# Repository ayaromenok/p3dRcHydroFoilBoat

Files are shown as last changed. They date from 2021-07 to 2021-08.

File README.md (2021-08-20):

# 3D printed Radio Controlled Hydrofoil boat

## Table of Contents

 - [Introduction](#intro)
 - [Status - on hold](#on_hold)
 - [Version v0.3.0](#v0_3_0)
 - [Version v0.2.0](#v0_2_0)
 - [Version v0.1.1](#v0_1_1)

## Introduction

Hydrofoil boat (called "Meteor" in tribute of Rostislav Alexeev hydrofoil ship) with trimaran structure and differentional trust mix props.
Impelented in OpenSCAD. To rebuild STL's required [p3d Lib2 0.2.2.20210615](https://github.com/ayaromenok/p3dLib)

## Status - on hold

Due to instability of boat in hydrofoil mode current development is put on hold. New ideas about form of wing required

## v0.3.0 

- Version from 2021.08.20

### Issues
  - stability issues in hydrofoil mode
  - CoPET printed floats not hydroscopic

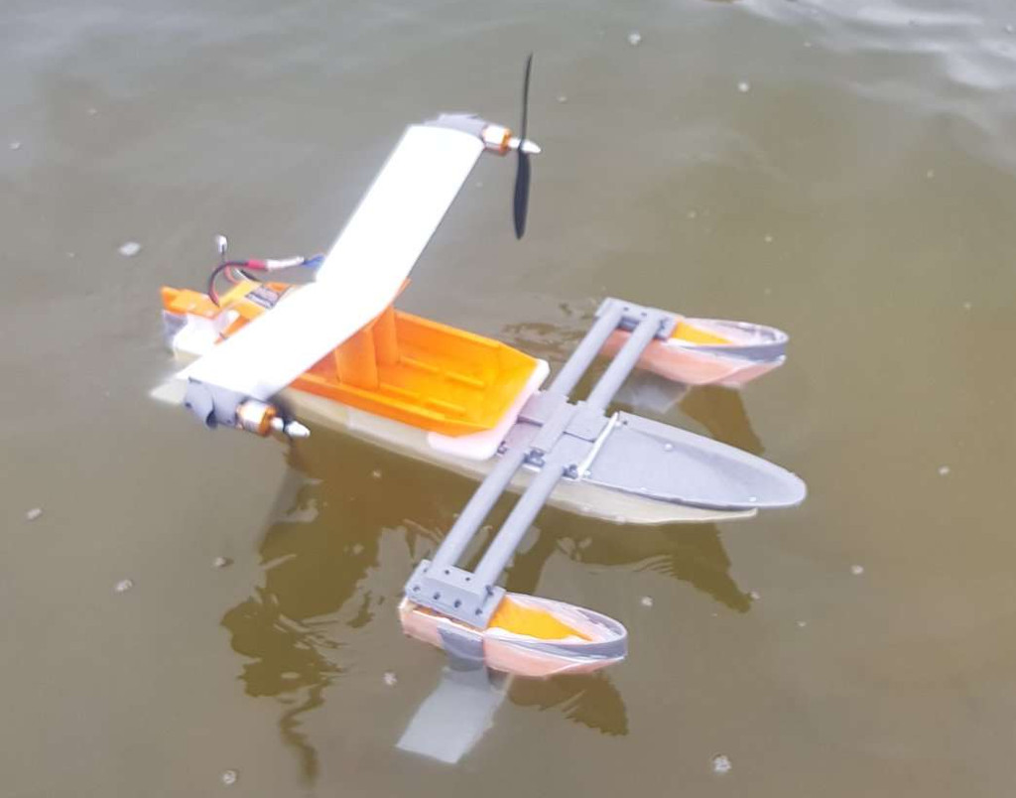
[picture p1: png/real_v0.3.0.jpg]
    
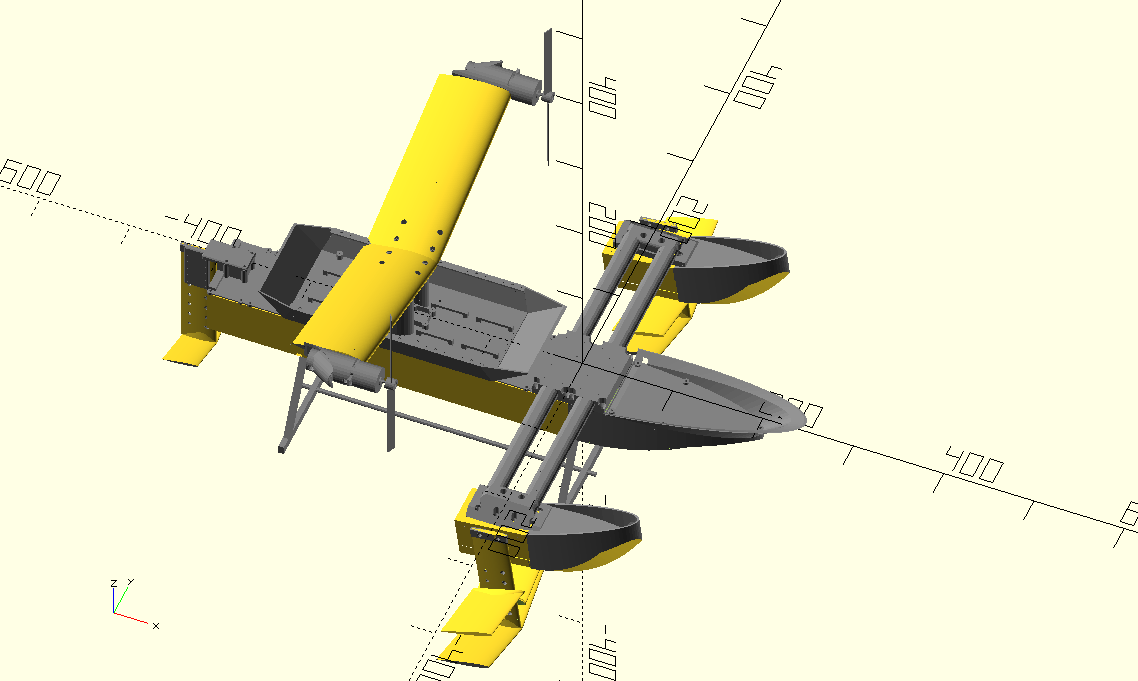
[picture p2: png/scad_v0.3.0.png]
    

## v0.2.0 

- Version from 2021.07.23

### Issues    
  - support float/hydrofoil connetors need to be higher(affected by water)
  - line of support floats and engine should be in one line (spray affected props)
  - front connectors should be stronger
  - front floats should be installed in 10-15 degree
  - front wing can be bigger
  - camera connector should be mounted a top of the engine wings and be strong
  - nose gunwale(falschbort) should be much higher for strong wind situation
  
[video from ground](https://www.youtube.com/watch?v=aogEewLZsBY)
[onboard video](https://www.youtube.com/watch?v=OHG-W-Ka8qo)

## v0.1.1 

- Version from 2021.07.18

### Issues
  - waterproofness of right support float (printing issue)
  - small support floats [issue #8](https://github.com/ayaromenok/p3dRcHydroFoilBoat/issues/8)
  - support floats should be moved forward [issue #9](https://github.com/ayaromenok/p3dRcHydroFoilBoat/issues/9)
  - fuselage strength and connection need to be revisioned [issue #10](https://github.com/ayaromenok/p3dRcHydroFoilBoat/issues/10)
  - support for Jetson Nano carrier board required (wider fuselage required) [issue #10](https://github.com/ayaromenok/p3dRcHydroFoilBoat/issues/10)
  - support for Raspberry Pi required [issue #10](https://github.com/ayaromenok/p3dRcHydroFoilBoat/issues/10)
  
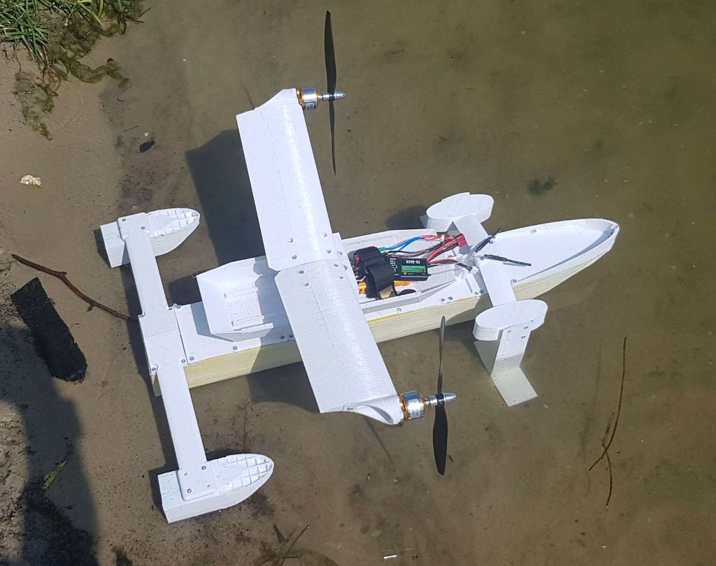
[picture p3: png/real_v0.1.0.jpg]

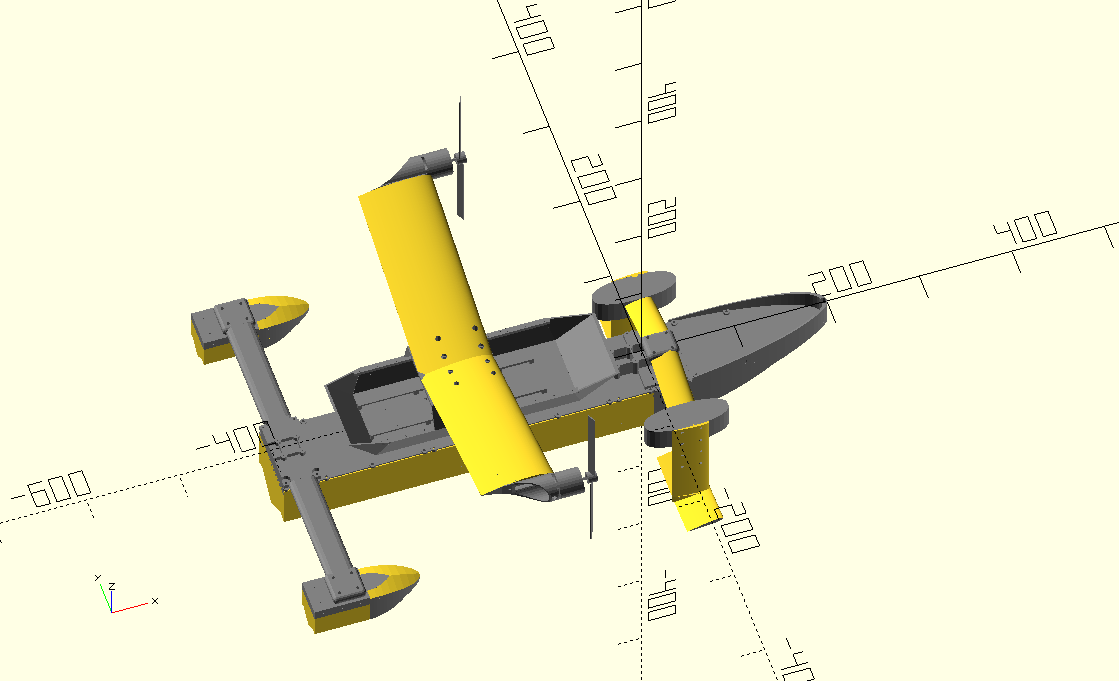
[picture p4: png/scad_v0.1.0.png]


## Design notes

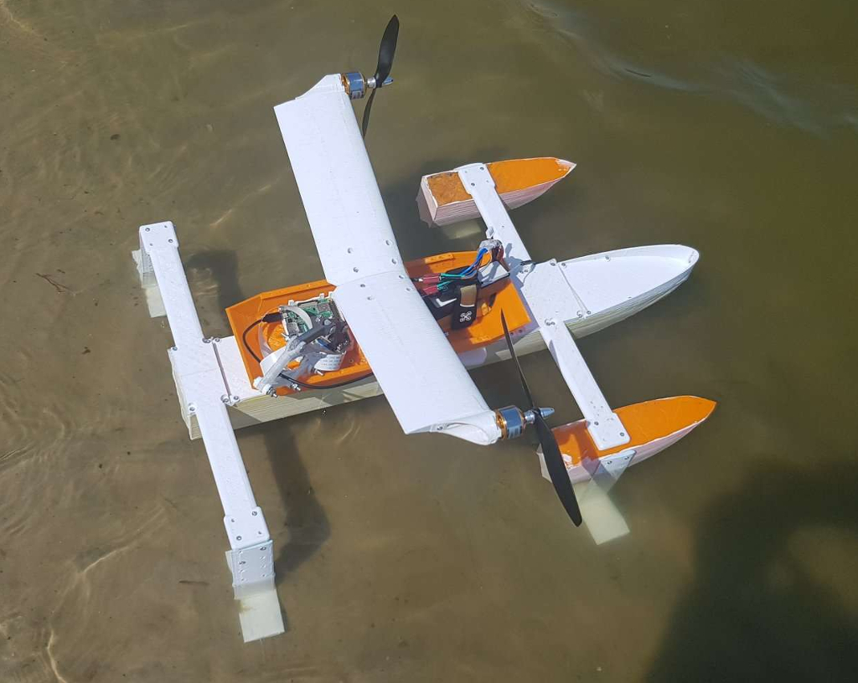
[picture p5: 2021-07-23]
png/real_v0.2.0.jpg

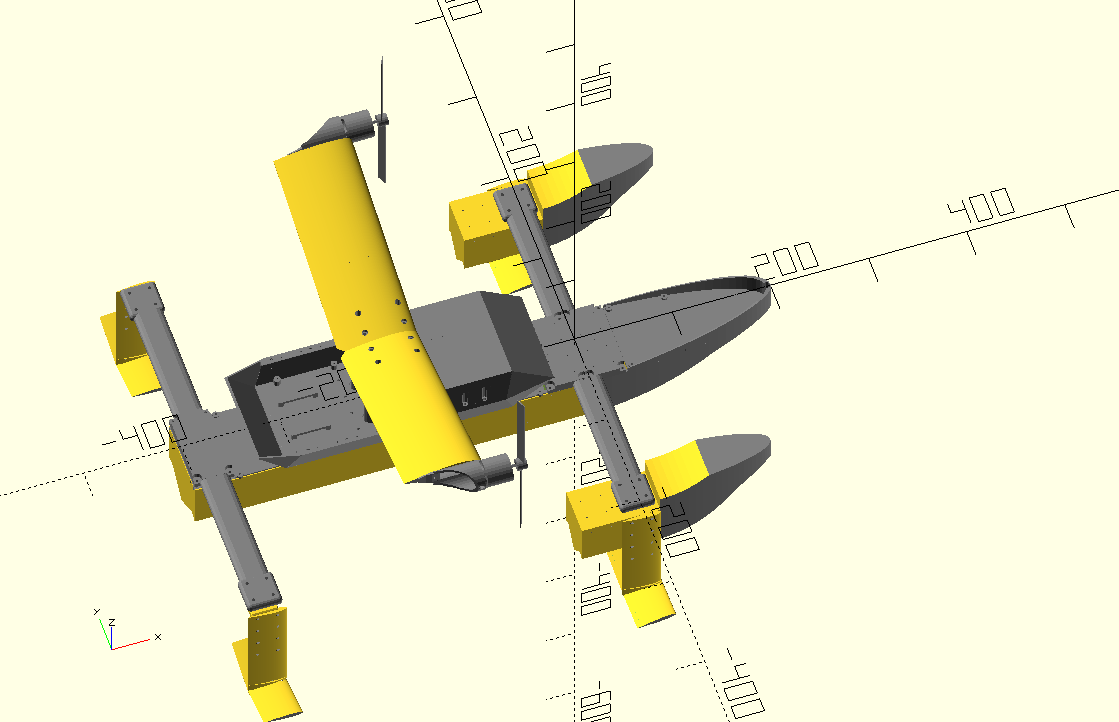
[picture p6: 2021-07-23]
png/scad_v0.2.0.png

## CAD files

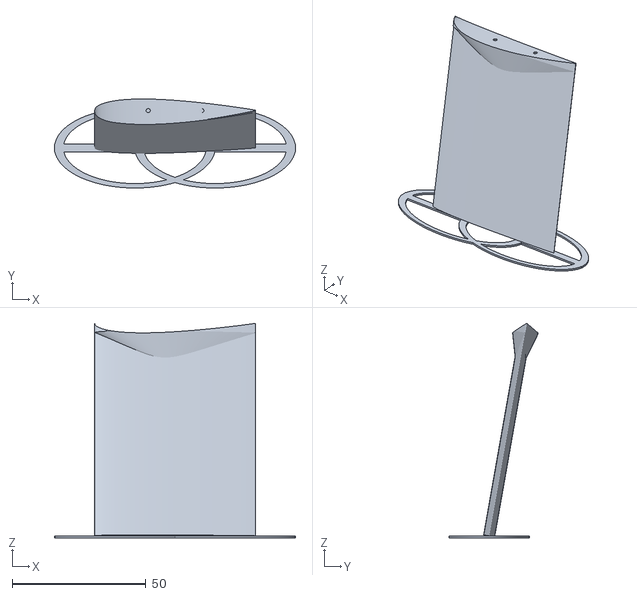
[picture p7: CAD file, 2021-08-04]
stl/wingHalf_80x60mm_L.stl
90.0 x 33.2 x 80.2

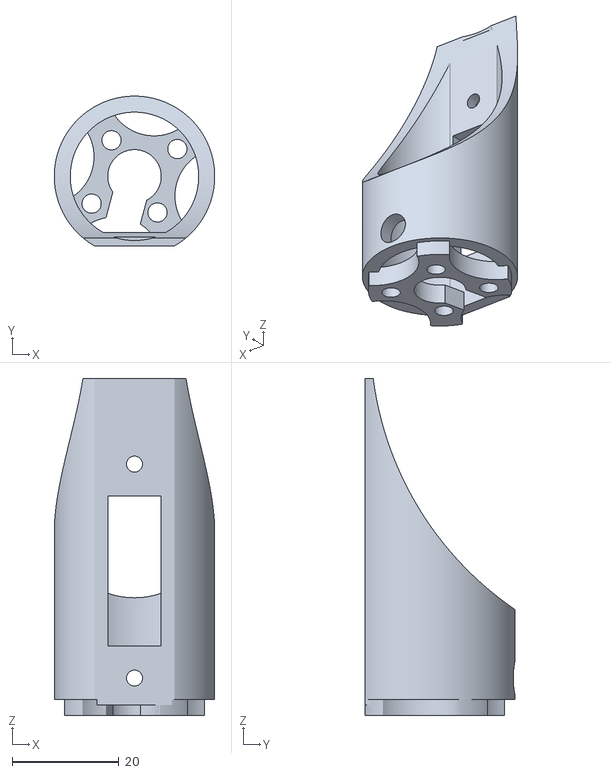
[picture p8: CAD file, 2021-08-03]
stl/engine2212_mount.stl
30.0 x 28.0 x 63.0

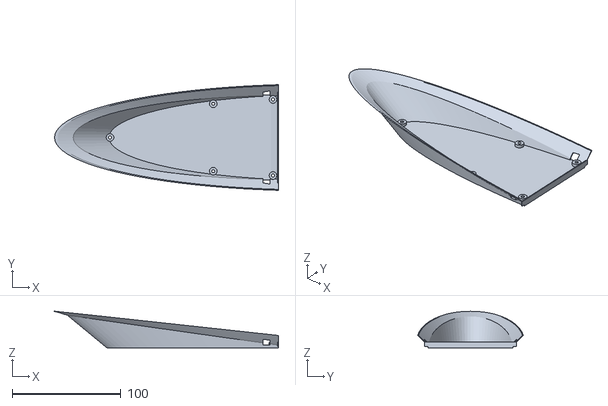
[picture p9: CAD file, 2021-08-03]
stl/floatsHiSpeed_v2_front_top.stl
206.2 x 97.3 x 33.6

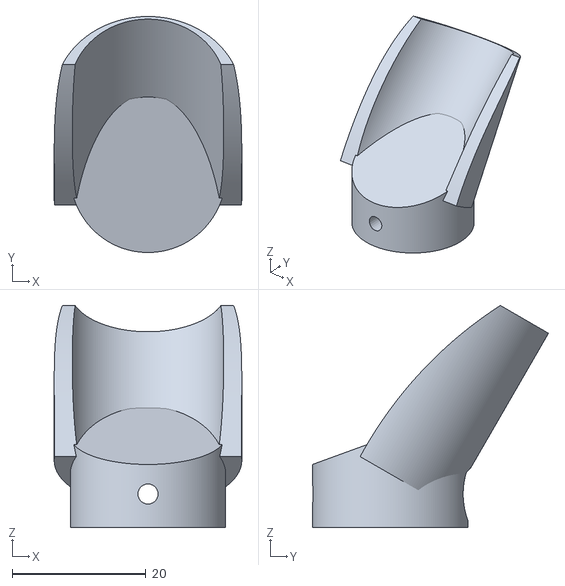
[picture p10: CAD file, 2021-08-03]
stl/dual2212MotorMount_ESC_air_intake.stl
28.0 x 35.2 x 33.1

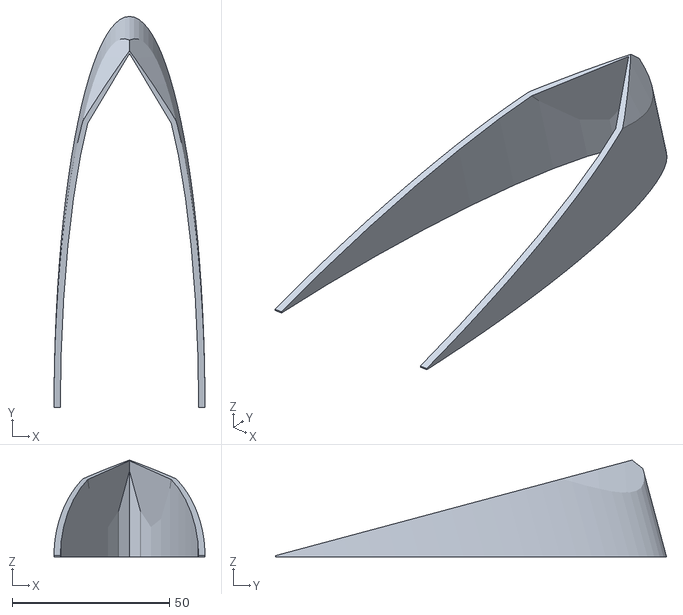
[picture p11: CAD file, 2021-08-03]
stl/floatsSupport_top.stl
48.0 x 124.3 x 30.8

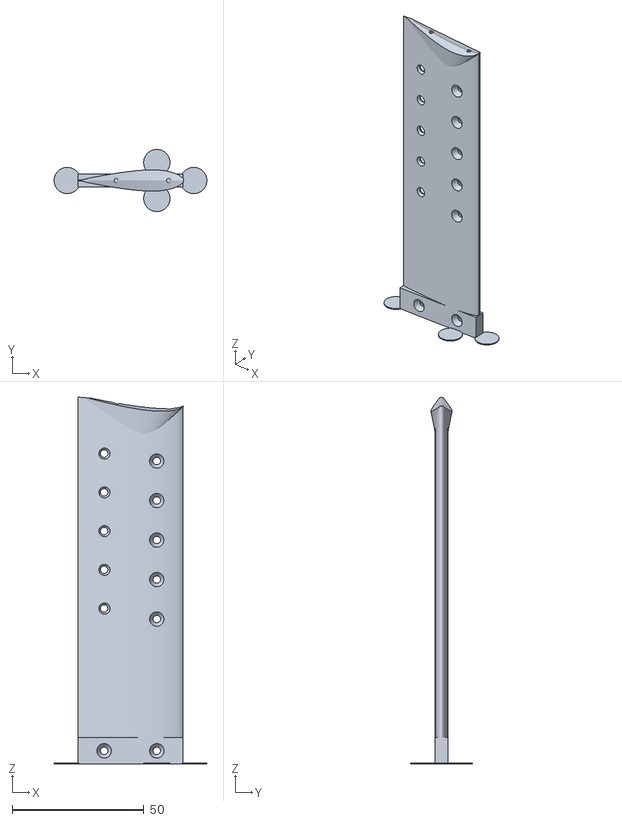
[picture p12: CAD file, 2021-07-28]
stl/wingHolder_140mm.stl
58.0 x 23.6 x 139.3

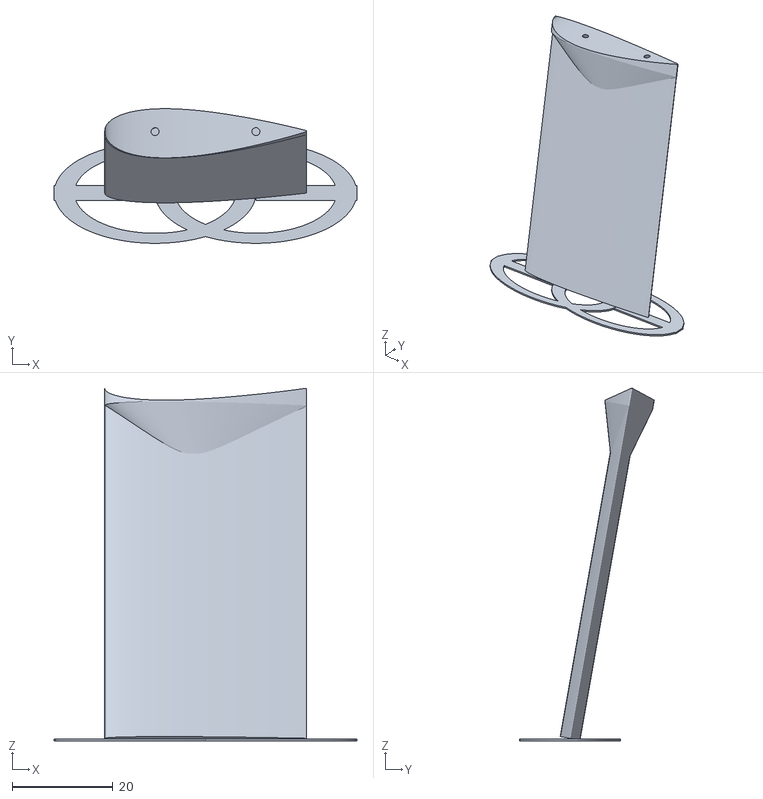
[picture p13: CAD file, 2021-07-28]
stl/wingHalf_70x40mm_L.stl
60.0 x 26.7 x 70.0

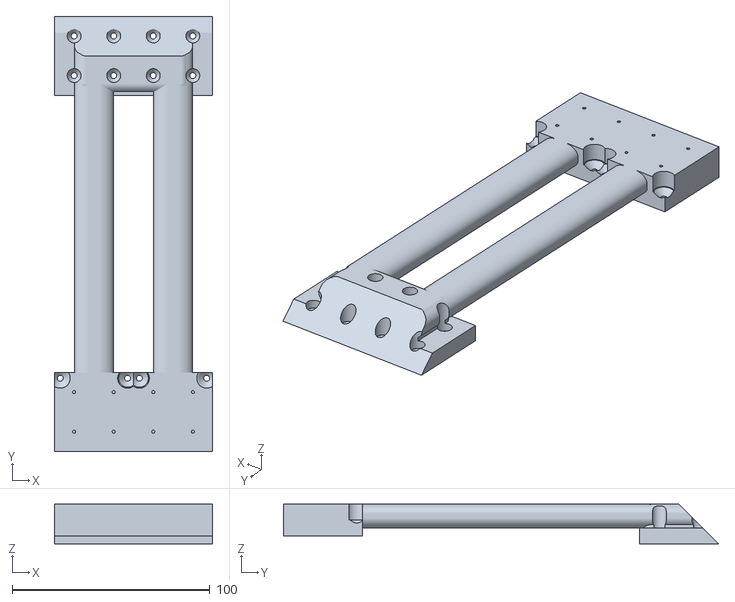
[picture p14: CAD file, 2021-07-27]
stl/floatsSupportFront_v3.stl
80.0 x 219.9 x 20.0

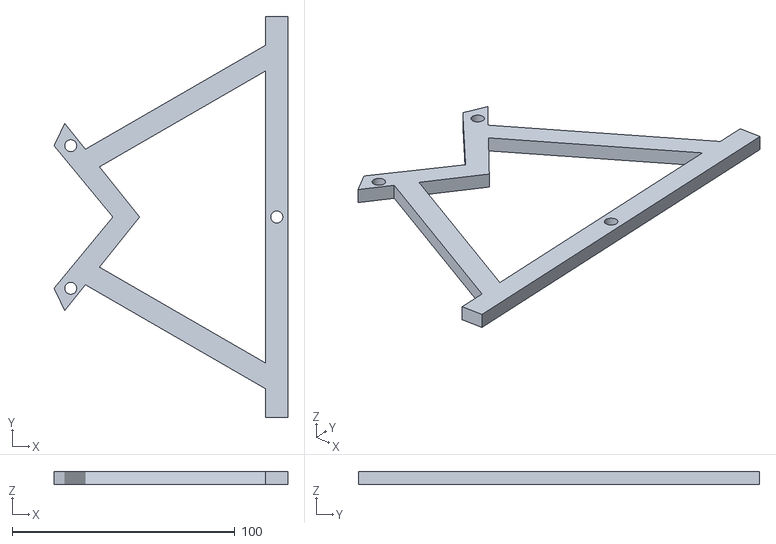
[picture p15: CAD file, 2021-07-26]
stl/floatsHiSpeed_v2_holder.stl
105.0 x 180.0 x 6.00

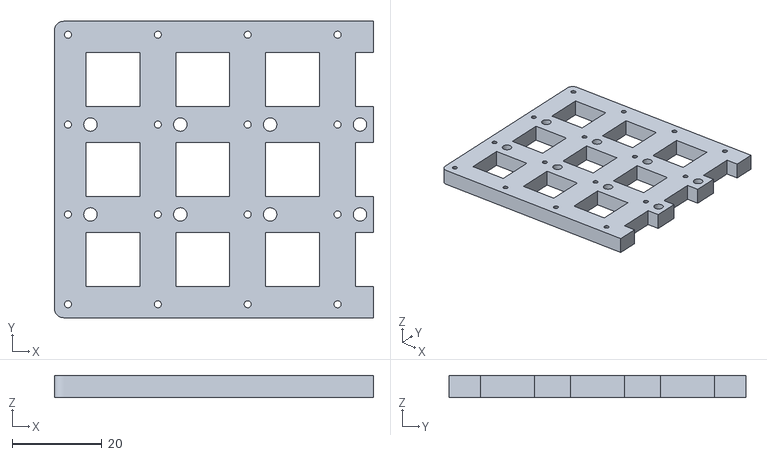
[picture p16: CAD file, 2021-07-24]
stl/fuselage_v2_front_back_support.stl
71.0 x 66.0 x 5.00

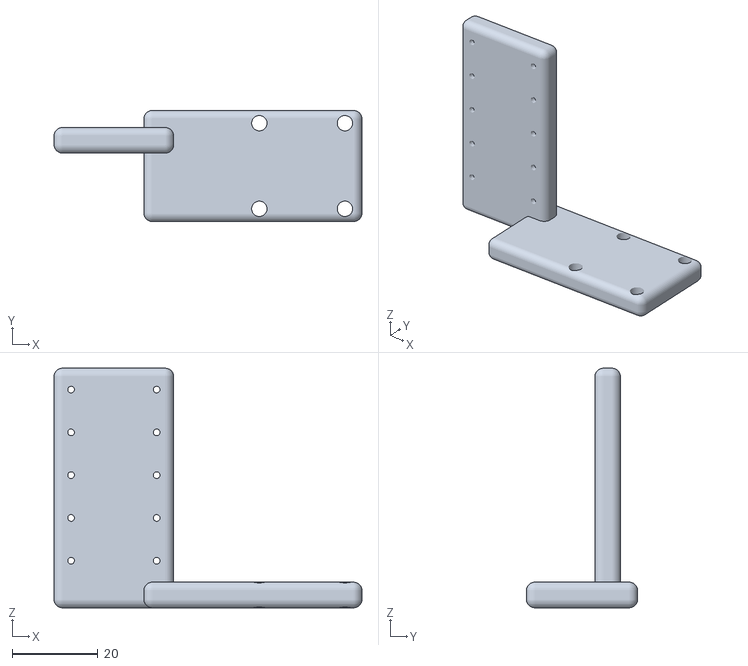
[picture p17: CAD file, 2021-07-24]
stl/wingHolderBack.stl
72.0 x 26.0 x 56.0

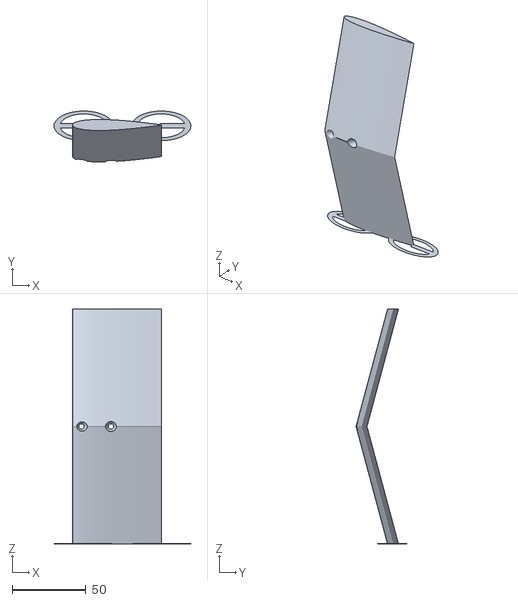
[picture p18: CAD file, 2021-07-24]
stl/wing_V15_160x60mm.stl
92.5 x 34.4 x 159.0

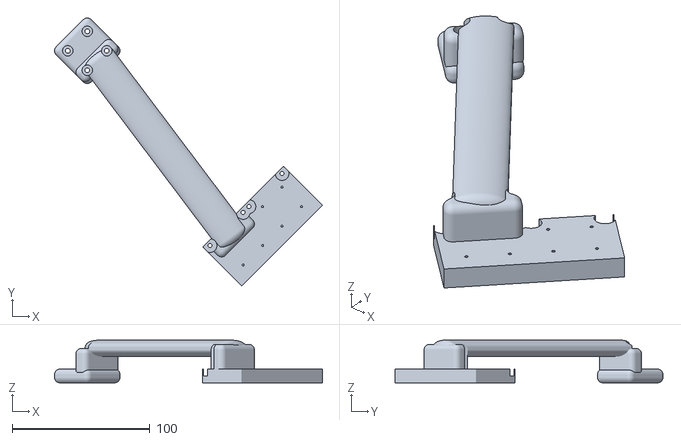
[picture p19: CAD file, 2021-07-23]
stl/floatsSupportFront_v2_mirrored.stl
194.6 x 194.6 x 31.0

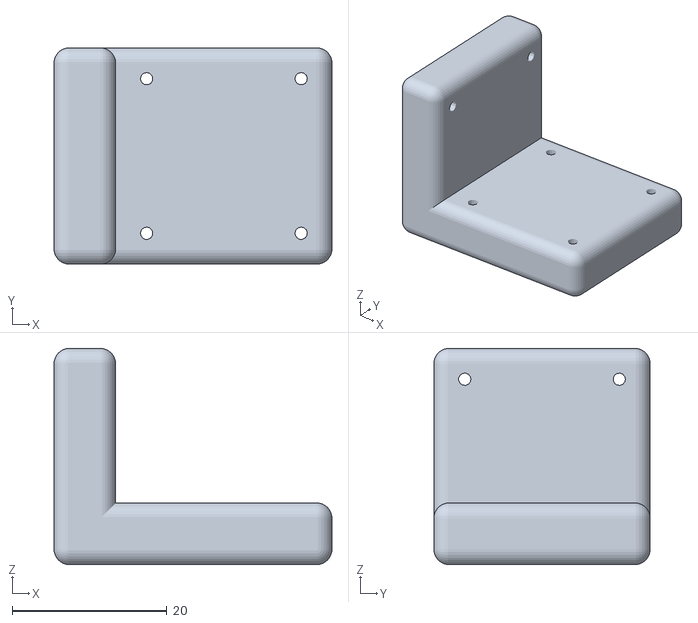
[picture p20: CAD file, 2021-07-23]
stl/floatsSupportConnector_L.stl
36.0 x 28.0 x 28.0

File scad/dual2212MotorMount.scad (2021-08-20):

include <../../lib/lib2.scad>
include <../../lib/lib2/ext/motor.scad>
include <../../lib/lib2/ext/prop.scad>
include <../../lib/lib2/ext/servo.scad>


//engine2212_wing();
//engine2212_mount(isMetal=false);
//engine2212_mount_ESC_air_intake();
//engine2212_mount_ESC_air_intake(27,-220,0,  0,-90,0);
//2print
//engine2212_wing(rx=-90,isAdhesion=true);//left
//engine2212_wing(rx=90,my=1,isAdhesion=true);//right
//engine2212_mount(ry=90);//left
//engine2212_mount(ry=90, my=1);//right

function naca_half_thickness(x,t) = 5*t*(0.2969*sqrt(x) - 0.1260*x - 0.3516*pow(x,2) + 0.2843*pow(x,3) - 0.1015*pow(x,4));
function naca_top_coordinates(t,n) = [ for (x=[0:1/(n-1):1]) [x, naca_half_thickness(x,t)]];
function naca_bottom_coordinates(t,n) = [ for (x=[1:-1/(n-1):0]) [x, - naca_half_thickness(x,t)]];
function naca_coordinates(t,n) = concat(naca_top_coordinates(t,n), naca_bottom_coordinates(t,n));

module engine2212_mount_ESC_air_intake(px=0,py=0,pz=0, rx=0,ry=0,rz=0, mx=0,my=0,mz=0, isMetal=false, isAdhesion=false){
    translate([(px), (py), pz])
    rotate([rx,ry,rz])
    mirror([mx,my,mz]){  
        difference(){
            yCyl(11.6,30, 0,218,27,  0,90,0);            
            yCyl(4,20,  -10,220,27,   90,0,0);
            yCyl(1.5,40,  -10,218,27,   90,0,0);
            yCube(20,50,25,  10,220,27,   0,0,-20);
        }//difference
        
        difference(){
            difference(){
                yCyl(14,30, 8,222,27,  -30,90,0);
                yCyl(11.6,35, 11.4,222,27,  -45,90,0);
            }//difference
            difference(){
                yCube(150,150,40, -34,268,27);
                yCyl(62,50, -34,268,27,  0,0,0);
            }//difference
            yCyl(4,20,  -10,220,27,   90,0,0);
        }//difference
        
    }//transform
}//module

module engine2212_mount(px=0,py=0,pz=0, rx=0,ry=0,rz=0, mx=0,my=0,mz=0, isMetal=false, isAdhesion=false){
    translate([(px), (py), pz])
    rotate([rx,ry,rz])
    mirror([mx,my,mz]){  
        translate([50,218,27])
        rotate([0,90,0]){            
                if (isMetal){
                    blMotor2212(0,0,0 ,0,0,-22.5-10);            
                    prop8060(0,0,25,   0,0,0);      
                }//isMetal    
                difference(){
                    union(){
                        blMotor2212_bot(0,0,0, 0,0,-22.5-10);   
                        yTube(15,12,60, 0,0,-26-20,  0,0,0);
                        yCube(14,5,60,    0,-13,-45);
                    }//union                
                    yCyl(62,40, -0,50,-84,  0,90,0);
                    yCube(20,20,100,    0,-23,-50);
                    //holes - to engine mount            
                    yCyl(1.5,50,    0,0,-20,  90,0,0);
                    yCyl(1.5,50,    0,0,-60,  90,0,0);
                    yCyl(3,30,    0,20,-20,  90,0,0);
                    //
                    yCube(6.5,6,10, 1.5,-6,-15, 0,0,15);
                    yCube(10,10,28, 0,-10,-40, 0,0,0);
                    //yCube(6,10,18, 8.5,-10,-70, 0,17,0);
                    //yCube(6,10,18, -8.5,-10,-70, 0,-17,0);
                }//difference            
                
        }//translate        
    }//transform
}//module                

module engine2212_wing(px=0,py=0,pz=0, rx=0,ry=0,rz=0, mx=0,my=0,mz=0, isMetal=false, isAdhesion=false){
    translate([(px), (py), pz])
    rotate([rx,ry,rz])
    mirror([mx,my,mz]){  
        chord=80;
        length=210;
        difference(){
            union(){
                translate([chord/2,length/2,0])
                rotate([75,0,180])
                linear_extrude(height=length, center=true) {                    
                    points = naca_coordinates(t=0.22,n=300);
                    scale([chord,chord,1])
                        polygon(points);
                } //translate        
                
            }//union
            //cable to engine
            yCube(28,length+10,12,   10,length/2,0,  15,0,0);
            //vertical/horizontal geometry
            yCube(chord*2, chord,chord, 0,length+chord/2-5,0);
            yCube(chord*2, chord,chord, 0,-chord/2+5,0);            
            yCube(chord*2, chord,chord, 0,chord/2-5,-chord/2-25);
            
            //holes - to fuselage
            yCyl(1.8,70,    30,15,0);
            yCyl(1.8,70,    -10,15,0);
            yCyl(1.8,70,    30,35,0);
            yCyl(1.8,70,    -10,35,0);
        
            yCyl(3,20,    30,15,-10);
            yCyl(3,20,    -10,15,-10);
            yCyl(3,20,    30,35,-10);
            yCyl(3,20,    -10,35,-10);
            //holes - to engine mount            
            yCyl(0.8,50,    30,length,27,  90,0,0);
            yCyl(0.8,50,    -10,length,27,  90,0,0);
            
        }//difference
        
        if (isMetal){
            translate([50,length+9,27])
            rotate([0,90,0]){            
                blMotor2212(0,0,0 ,0,0,-22.5-10);            
                prop8060(0,0,25,   0,0,0);      
            
                //blMotor2212_bot(0,0,0, 0,0,-22.5-10);   
                //yTube(14,12,20, 0,0,-26,  0,0,0);
            }//translate
        }//isMetal
        if(isAdhesion){
            yCyl(5,0.7,    30,length-5.3,15,  90,0,0);
            yCyl(5,0.7,    -10,length-5.3,17,  90,0,0);
            yCyl(5,0.7,    -40,length-5.3,25,  90,0,0);        
        }//isAdhesion            
    }//transform
}//module                


//engine2212_basket_inch5_assembly();

//2print
//engine2212_basket_inch5_front();
//engine2212_basket_inch5_back();
//engine2212_support(0,0,0, 0,0,45);
//engine2212_basket_inch5_rudder(0,0,0, 0,90,90, isAdhesion=true);
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

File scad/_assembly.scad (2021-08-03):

include <hydrofoil.scad>
include <floatsHiSpeed_v2.scad>
include <dual2212MotorMount.scad>
include <fuselage_v2.scad>
include <floatsSupport.scad>

floatHiSpeed_v2_assmebly(0,0,39.5, 0,0,-90);
//float holder
floatHiSpeed_holder(0,0,-66, 0,90,90);
floatHiSpeed_holder(-300,0,-66, 0,90,90);
yCyl(2.5,330,   -150,0,-165,  0,90,0);

//engine wing
fuselage_engine_support(-200,0,-15);
engine2212_wing(-200,-5,110 );
engine2212_wing(-200,5,110, my=1);
engine2212_mount(-200,-5,110,isMetal=true);
engine2212_mount(-200,5,110,isMetal=true, my=1);
engine2212_mount_ESC_air_intake(-200,-5,110);
engine2212_mount_ESC_air_intake(-200,5,110, my=1);


//front hydro-wing
floatSupportWingFront_v3(0,0,-20, mx=1);
floatSupportWingFront_v3(0,0,-20, rz=180, mx=0);
floatSupport(20,-200,53,  7,0,-90);
floatSupport(20,200,49,  7,0,-90);
floatSupport_top(20,-200,53,  7,0,-90);
floatSupport_top(20,200,49,  7,0,-90);
wingMainNACA_multy_V_v2(7,-230,-164, 0,-7,0);
wingMainNACA_multy_V_v2(7,230,-164, 0,-7,0, 0,1,0);
//wingMainNACA_V(20,187,-133, 90,10,180, length=160,chord=60);
//wingHolderSingle(0,226,-145,  180,190,180, length=120);

//wingMainNACA_V(20,-265,-133, 90,10,180, length=160,chord=60);
//wingHolderSingle(0,-226,-145,  180,180,180, length=120);

//back hydro-wing
wingHolderBack(-385, rx=180);
wingMainNACA_V(-405,-25,-132,rx=90,ry=8, rz=180, isAdhesion=false, length =100, chord=40);
wingHolderSingle(-425,0,-143,isAdhesion=false);

//fuselage
//fuselage_front_back_support(-200,0,2.5);
fuselage_front(-200,0,-10);
fuselage_back(-310,0,-10);

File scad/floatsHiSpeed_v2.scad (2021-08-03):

include <../../lib/lib2.scad>

//2print rotated in Y axis for better print
//floatHiSpeed_front_v2(pz=-60,ry=-90,rz=0);
//floatHiSpeed_front_top_v2(ry=-90,rz=0);
//floatHiSpeed_center_v2(pz=-60,ry=-90,rz=0);
//floatHiSpeed_front_top_v2_1(ry=-90,rz=90);
//floatHiSpeed_front_top_v2_1_1(ry=-90,rz=90);
//floatHiSpeed_front_top_v2_1_1(-42,0,0, 90,(90-6.2),0);
//floatHiSpeed_front_top_v2_1_1(-42,0,0, 90,-90,0);
//floatHiSpeed_front_top_v2_1_2(ry=-90,rz=0);
//floatHiSpeed_center_top_v2_1(ry=-90,rz=0);
//floatHiSpeed_center_top_v2_3(ry=-90,rz=0);
//floatHiSpeed_v2_assmebly();

//floatHiSpeed_holder(rx=90);

module floatHiSpeed_holder(px=0,py=0,pz=0, rx=0,ry=0,rz=0){
    translate([(px),(py),pz])
    rotate([rx,ry,rz]){
            difference(){                                        
                scale([1.2,1,1])            
                rotate([90,0,0])
                linear_extrude(6)
                    polygon( points=[[0,32],[22,0],[0,-32], [4,-42],[32,0], [4,42]]);
                yCyl(2.7,20,    7.5,0,32,  90,0,0);
                yCyl(2.7,20,    7.5,0,-32,  90,0,0);
            }//difference
        yCube(100,6,10,  58,-3,50, 0,-30,0);
        yCube(100,6,10,  58,-3,-50,  0,30,0);
        difference(){    
            yCube(10,6,180,  100,-3,0);    
            yCyl(2.7,20,    100,0,0,  90,0,0);    
        }//difference
    }//transform
}//module                    
module floatHiSpeed_v2_assmebly(px=0,py=0,pz=0, rx=0,ry=0,rz=0){
    translate([(px),(py),pz])
    rotate([rx,ry,rz])
        rotate([0,90,0])
    {
        floatHiSpeed_front_v2();//132
        //floatHiSpeed_front_top_v2();
        floatHiSpeed_center_v2();
        floatHiSpeed_center_v2(0,-200,0);
        floatHiSpeed_front_top_v2_1_1(142,0,0,    0,180);
        //floatHiSpeed_front_top_v2_1_2(142,0,0,    0,180);
        floatHiSpeed_center_top_v2_1(142,0,0,    0,180);
        floatHiSpeed_center_top_v2_2(142,-200,0,    0,180);
        floatHiSpeed_center_top_v2_1(142,-200,0,    0,180);
        floatHiSpeed_center_top_v2_3(142,-400,0,    0,180);
    }//transform
}//module


module floatHiSpeed_center_top_v2_3(px=0,py=0,pz=0, rx=0,ry=0,rz=0){
    translate([(px),(py),pz])
    rotate([rx,ry,rz])    
    {
        difference(){
            floatHiSpeed_center_top_v2_2();
            yCube(30,50,100,   90,-25);
        }
    }//transform
}//module


module floatHiSpeed_center_top_v2_1(px=0,py=0,pz=0, rx=0,ry=0,rz=0){
    translate([(px),(py),pz])
    rotate([rx,ry,rz])    
    {
    difference(){        
            yCube(3,116,78,    82,-100,0);
            //connectors            
            yCyl(1.5,26,  80,-47,37, 0,90,0);
            yCyl(1.5,26,  80,-47,-37, 0,90,0);
            yCyl(1.5,26,  80,-103,37, 0,90,0);
            yCyl(1.5,26,  80,-103,-37, 0,90,0);          
            yCyl(1.5,26,  80,-153,37, 0,90,0);
            yCyl(1.5,26,  80,-153,-37, 0,90,0); 
        }//difference
        yTube(3.5,1.5,3,  83,-47,37, 0,90,0);
        yTube(3.5,1.5,3,  83,-47,-37, 0,90,0);
        yTube(3.5,1.5,3,  83,-103,37, 0,90,0);
        yTube(3.5,1.5,3,  83,-103,-37, 0,90,0);          
        yTube(3.5,1.5,3,  83,-153,37, 0,90,0);
        yTube(3.5,1.5,3,  83,-153,-37, 0,90,0); 
        
    }//transform
}//module



module floatHiSpeed_center_top_v2_2(px=0,py=0,pz=0, rx=0,ry=0,rz=0){
    translate([(px),(py),pz])
    rotate([rx,ry,rz])    
    {
    difference(){        
            yCube(3,84,78,    82,0,0);
            //connectors            
            yCyl(1.5,26,  80,37,37, 0,90,0);
            yCyl(1.5,26,  80,37,-37, 0,90,0);
            yCyl(1.5,26,  80,3,37, 0,90,0);
            yCyl(1.5,26,  80,3,-37, 0,90,0);          
            yCyl(1.5,26,  80,-3,37, 0,90,0);
            yCyl(1.5,26,  80,-3,-37, 0,90,0); 
            yCyl(1.5,26,  80,-37,37, 0,90,0);
            yCyl(1.5,26,  80,-37,-37, 0,90,0);          
        
        }//difference
        yTube(3.5,1.5,3,  83,37,37, 0,90,0);
        yTube(3.5,1.5,3,  83,37,-37, 0,90,0);
        yTube(3.5,1.5,3,  83,3,37, 0,90,0);
        yTube(3.5,1.5,3,  83,3,-37, 0,90,0);          
        yTube(3.5,1.5,3,  83,-3,37, 0,90,0);
        yTube(3.5,1.5,3,  83,-3,-37, 0,90,0); 
        yTube(3.5,1.5,3,  83,-37,37, 0,90,0);
        yTube(3.5,1.5,3,  83,-37,-37, 0,90,0);          
        yCube(5,16,70,    85.5,,-0);
        for (i=[-30:20:40]){
            yTube(3.5,0.7,20,    92.5,i,10, 0,90,0);
            yTube(3.5,0.7,20,    92.5,i,-10,0,90,0);
            yCube(20,1,18,    92.5,i,0);
            yCube(20,1,18,    92.5,i,00);
         }//for
         for (i=[-20:20:20]){
            yCube(20.0,18,1,    92.5,i,10);
            yCube(20.0,18,1,    92.5,i,-10);
         }//for    
    }//transform
}//module

module floatHiSpeed_front_top_v2_1_1(px=0,py=0,pz=0, rx=0,ry=0,rz=0){
    translate([(px),(py),pz])
    rotate([rx,ry,rz])    
    {
        difference(){
            union(){
                yCyl(0,33, 98,0,0,  0,90,0, $fn=100, sy=5,rb=40, rt=48);
                yCyl(0,10, 84,0,0,  6,90,0, $fn=100, sy=5,rb=40, rt=50);                
            }//union
            yCyl(0,32, 100,0,0,  0,90,0, $fn=100, sy=5, rb=39.6,rt=47.6);
            yCyl(0,10.2, 84,0,0,  6,90,0, $fn=100, sy=5.03,rb=39.2, rt=49.2);
            yCube(130,370,150,    108,-143,0);
            yCube(30,250,150,    119,144,0, 0,0,-6.2);
            //connectors
            yCyl(3.5,26,  98,196,0, 0,90,0);
            yCyl(1.4,26,  80,197,0, 0,90,0);
            yCyl(1.4,26,  80,102,31, 0,90,0);
            yCyl(1.4,26,  80,102,-31, 0,90,0);
            yCyl(1.4,26,  80,47,35, 0,90,0);
            yCyl(1.4,26,  80,47,-35, 0,90,0);          
            //water pass
            yCube(5,6,86,    86.5,53,0);
            //top light
            yCyl(2,100, 111,155,0, 0,0,0);
            yCyl(3,100, 110,145,0, 0,0,0);
            yCyl(2,100, 108,135,0, 0,0,0);
        }//difference
        //central support section
        /*difference(){
            yCube(30,152,2,    97,118,0);
            yCube(30,250,150,    119,144,0, 0,0,-6.2);
        }//difference
        */
        yTube(3.5,1.4,3,  85,197,0, 0,90,0);
        yTube(3.5,1.4,3,  85,102,31, 0,90,0);
        yTube(3.5,1.4,3,  85,102,-31, 0,90,0);
        yTube(3.5,1.4,3,  85,47,35, 0,90,0);
        yTube(3.5,1.4,3,  85,47,-35, 0,90,0);
        yCube(4,0.7,85,    84.8,42.3,0);        
        
        //yCube(5,80,5,    105,105,39, 0,45,-17);
    }//transform
}//module
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

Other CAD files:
stl/wingHalf_80x60mm_R.stl
stl/wingHalf_70x40mm_R.stl
stl/fuselage_v2_back.stl
stl/fuselage_v2_front_top.stl
scad/floatsSupport.scad
scad/floatsSupport_v2.scad
scad/fuselage.scad
scad/fuselage_v2.scad
scad/hydrofoil.scad
stl/engine2212_wing_left.stl
stl/engine2212_wing_right.stl
stl/floatsSupport.stl
stl/floatsSupportFront.stl
stl/floatsSupportFront_v2.stl
stl/floatsSupportWIng.stl
stl/floatsSupportWingFront.stl
stl/fuselage_back_bot.stl
stl/fuselage_front_bot.stl
stl/fuselage_v2_engine_support.stl
stl/fuselage_v2_front.stl
stl/wingChassis.stl
stl/wingHolder_120mm.stl
stl/wing_V15_100x40mm.stl

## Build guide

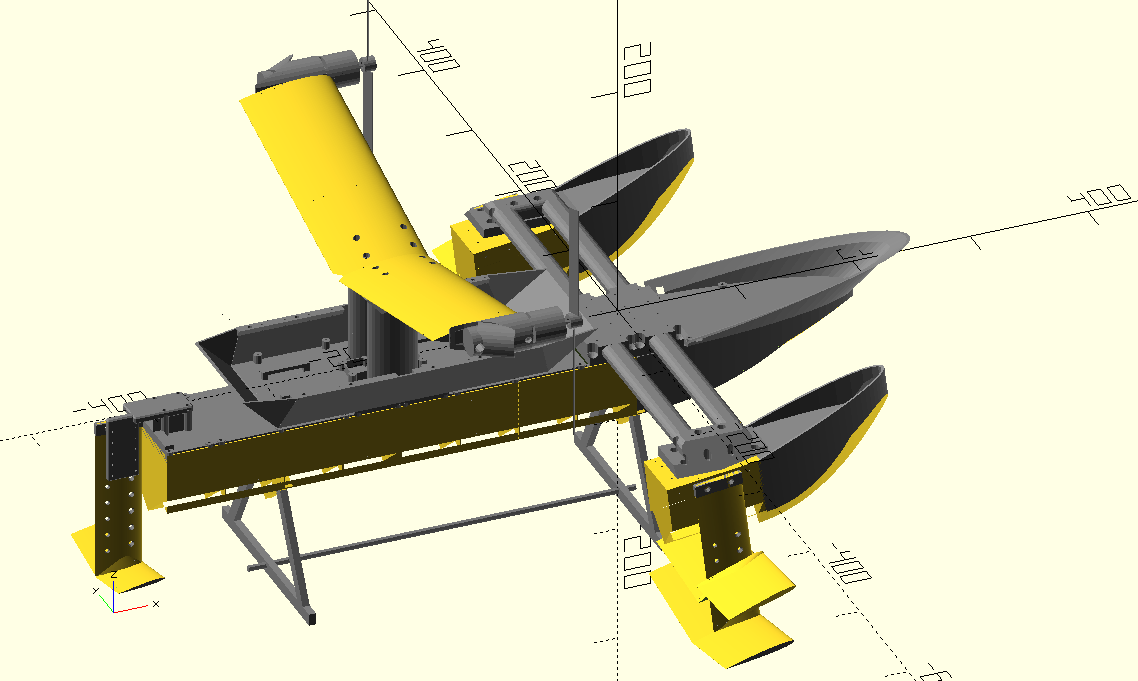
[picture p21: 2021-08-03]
png/_assembly.png

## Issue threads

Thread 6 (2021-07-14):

Fuselage for dual engine mount

ayaromenok, 2021-07-14:
can be connected to single or dual float configuration

ayaromenok, 2021-07-17:
need to review bottom section(thickness and connectors),
 make it more wide(to hold nvidia jetson nano)

Closed 2021-07-18.

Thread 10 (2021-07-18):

new fuselage (V2)

ayaromenok, 2021-07-18:
- better connector to main float
- Jetson nano carrier board connector
- Raspberry Pi  board connector

Closed 2021-07-23.

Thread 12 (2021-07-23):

higher angled connector to suppor floats/wings

ayaromenok, 2021-07-23:
- Current affected to much by the water/sprays from nose
- angle to floats need to be added on front

Closed 2021-07-26.

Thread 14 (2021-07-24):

switch to 3 wings/props ahead version

ayaromenok, 2021-07-24:
after evaluation is looks like too much water affect props - so need to move them in front

ayaromenok, 2021-07-27:
prop ahead is not a good idea for this size on main float - weight is too big

Closed 2021-07-27.

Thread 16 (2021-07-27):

stronger engine mount

ayaromenok, 2021-07-27:
in case of touching water/spray engine mount can be broken - so stronger construction required

Closed 2021-07-27.

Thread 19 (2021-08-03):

ESC Air Intake

ayaromenok, 2021-08-03:
after burning one ESC(and a motor as a result) it's looks like a good idea to tame some air and send inside  to engine wings to cool ESC

Closed 2021-08-03.

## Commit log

2021-07-14 #2 added wing(100mm) with V=15 degree and 100mm holder
    [hydrofoil.scad, wingHolder_100mm.stl, wing_V15_100mm.stl]
2021-07-14 #4 used speed boat v2
    [floatsHiSpeed_v2.scad]
2021-07-14 #1 assembly added
    [_assembly.scad]
2021-07-14 #2 #3 - updated wing, including small float support
    [hydrofoil.scad, wingChassis.stl, wingHolder_100mm.stl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]
2021-07-14 #1 updated assmebly
    [_assembly.scad]
2021-07-14 #5 first version of dual-engine mount, suitable even fo 10inch props
    [dual2212MotorMount.scad, engine2212_mount_left.stl, engine2212_mount_right.stl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]
2021-07-14 #1 assembly updated with dual engine mount
    [_assembly.scad]
2021-07-15 #5 engine mount modfied - used only one modelfor both
    [engine2212_mount.stl, engine2212_mount_left.stl, engine2212_mount_right.stl]
2021-07-15 #5 fixed scad
    [dual2212MotorMount.scad]
2021-07-15 #6 fuselage front
    [fuselage.scad, fuselage_front_bot.stl]
2021-07-15 #1 fuselage added
    [_assembly.scad]
2021-07-15 #6 fix battery holder
    [fuselage.scad, fuselage_front_bot.stl]
2021-07-15 #6 fuselage back section
    [fuselage.scad, fuselage_back_bot.stl]
2021-07-15 #6 thicknes fixed
    [fuselage.scad, fuselage_back_bot.stl, fuselage_front_bot.stl]
2021-07-17 #2 added more connector holes, and 140mm version
    [hydrofoil.scad, wingHolder_140mm.stl]
2021-07-17 #7 #1 added support floats
    [_assembly.scad, floatsHiSpeed_v2.scad, floatsSupport.scad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]
2021-07-17 #7 #1 float support wing added
    [_assembly.scad, floatsSupport.scad, floatsSupport.stl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]
2021-07-18 #7 updated support floats
    [floatsSupport.scad, floatsSupport.stl]
2021-07-18 updated to v0.1.0
    [floatsSupport.scad]
2021-07-19 #8 bigger support floats
    [floatsSupport.scad, floatsSupport.stl, floatsSupportFront.stl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]
2021-07-19 #1 assembly updated with bigger support floats(#8)
    [_assembly.scad]
2021-07-20 #10 fuselage v2 with jetson nano/rpi connectors
    [fuselage_v2.scad, fuselage_v2_back.stl, fuselage_v2_engine_support.stl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]
2021-07-20 #1 assembly with fuselage v2 updated
    [_assembly.scad]
2021-07-22 #10 updated with additional holes
    [fuselage_v2.scad, fuselage_v2_back.stl, fuselage_v2_engine_support.stl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]
2021-07-22 #5 engine mount make more stronger
    [dual2212MotorMount.scad, engine2212_mount.stl]
2021-07-22 #7 added L-connector
    [floatsSupport.scad, floatsSupportConnector_L.stl]
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2021-07-23 #10 updated bottom and top sections
    [fuselage_v2.scad, fuselage_v2_back.stl, fuselage_v2_front_top.stl]
2021-07-23 #7 correct connectors for back wings
    [floatsSupportConnector_L.stl]
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2021-07-23 #11 bigger wings 160x60 - 2.25 times
    [_assembly.scad]
2021-07-23 #11 160x60 V-like wings
    [hydrofoil.scad, wing_V15_160x60mm.stl]
2021-07-23 #12 higher and longer front support connectors
    [floatsSupport.scad, floatsSupportFront_v2.stl, floatsSupportFront_v2_mirrored.stl]
2021-07-23 #12 #1 assmebly updated with new support float wings
    [_assembly.scad, floatsSupport.scad]
2021-07-24 #13 floatHiSpeed_front_top_v2_1_1 added, but may be require another solution
    [floatsHiSpeed_v2.scad]
2021-07-24 #11 added hiding plcae for scruls
    [hydrofoil.scad, wing_V15_160x60mm.stl]
2021-07-24 #13 #1 switch to 3-wing configuration
    [_assembly.scad, floatsHiSpeed_v2.scad, hydrofoil.scad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]
2021-07-24 #13 #1 #10 updated to fuselage/assmbly due to #13
    [_assembly.scad, fuselage_v2.scad, fuselage_v2_front_back_support.stl]
2021-07-24 #13 updated floatd support wings
    [floatsSupport.scad, floatsSupportFront_v3.stl]
2021-07-24 #13 #1 version with 3 big wings
    [_assembly.scad]
2021-07-26 #15 main float holder
    [floatsHiSpeed_v2.scad, floatsHiSpeed_v2_holder.stl]
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2021-07-26 #1 assembly updated with holder for main float
    [_assembly.scad]
2021-07-27 #14 stronger front float wings
    [floatsSupport.scad, floatsSupportFront_v3.stl]
2021-07-27 #16 stronger engien mount
    [_assembly.scad, engine2212_mount.stl]
2021-07-27 #1 updated assmebly with stronger support floats wing and engine mount
    [_assembly.scad, dual2212MotorMount.scad]
2021-07-28 #17 multiwing 1st version - don't print well
    [hydrofoil.scad, wing_V15x3_100x40mm.stl]
2021-07-28 #17 milti-wing from parts
    [hydrofoil.scad, wingHalf_70x40mm_L.stl, wingHalf_70x40mm_R.stl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]
2021-07-28 #1 #17 multi-wing from parts added to assembly
    [_assembly.scad]
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2021-08-03 #13 bigger gunwale fro support floats
    [floatsSupport.scad, floatsSupport_top.stl]
2021-08-03 #13 new hiSpeed float v2 fromt/top section
    [floatsHiSpeed_v2.scad, floatsHiSpeed_v2_front_top.stl]
2021-08-03 #3 assembly updated with new front tops waveshields #13
    [_assembly.scad]
2021-08-03 #19 ESC air intake
    [dual2212MotorMount.scad, dual2212MotorMount_ESC_air_intake.stl]
2021-08-03 #1 assembly updated with ESC air intakes(#19)
    [_assembly.scad]
2021-08-03 #13 updated for printing
    [floatsHiSpeed_v2.scad, floatsHiSpeed_v2_front_top.stl]
2021-08-03 #5 #13 small fixes
    [dual2212MotorMount.scad, engine2212_mount.stl, floatsHiSpeed_v2.scad]
2021-08-03 #17 multiwing updated to size 80x60mm/160x60mm
    [hydrofoil.scad, wingHalf_80x60mm_L.stl, wingHalf_80x60mm_R.stl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]
2021-08-03 #1 updated with bigger hydrofoil wings(#17)
    [_assembly.scad]
2021-08-04 #17 adhesion updated in half wing
    [hydrofoil.scad, wingHalf_80x60mm_L.stl, wingHalf_80x60mm_R.stl]
2021-08-20 #17 fix lib2 path
    [dual2212MotorMount.scad]
